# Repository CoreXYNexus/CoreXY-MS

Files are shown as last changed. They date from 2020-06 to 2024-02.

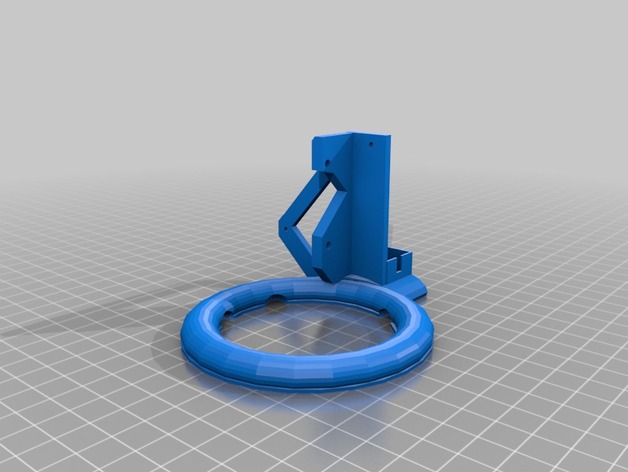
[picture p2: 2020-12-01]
STL/Other/Titan+Aero+Fan+shroud/images/5f8aa84927e1736dd930bd4a682ead06.png

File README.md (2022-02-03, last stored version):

# CoreXY-MS
A corexy printer using Makerslide, EXOSlide with Duet 3 6HC and 1LC using a Raspberry Pi 4.

August 2020: Upgraded to a Duet 3 6HC with 1LC.  Currently using in stand alone, no Pi.

A very old version is available at http://www.thingiverse.com/thing:1470253

https://creativecommons.org/licenses/by-sa/4.0/

https://youtu.be/llArYEVT2ow with Duet 2.
https://www.youtube.com/watch?v=qqqCqKSmpecVideo with the Duet 3.

All the horizontal extrusions, and the horizontal makerslide ends are tapped for 5mm.
Vertical 2020 is drilled with a 5.5mm bit for access to the screws that hold everything together. Four in the top and two in the bottom. Use drillguide.stl for drilling the holes.

Additional information can be found in the scad files. Include files are expected to be in a folder called inc in the folder with the printer's scad files.
In the top extrusions, I put 8 tnuts in each channel, the rest four in each. Use a short screw in a unused one to hold them to one side to quiet the rattle they can make while printing.

Spool holder: 300mm 2020 with two screw access holes in the bottom to mount it on the top rear 2040 and a 8mm hole in the top for a 8mm threaded rod long enough to hold a spool on each side. Using http://www.thingiverse.com/thing:1647748 to hold the spools.  The horizontal 2020 300mm long to hold filament guides for each spool.

On the bearing brackets from the top: M5x50, bearing support, washer, 2xF625Z,2x washers,2x F625Z, M5 nut.

If you use metal couplers for the z-axis, use a 4mm ball bearing in between the TR8 and stepper motor shaft inside the coupler. The bearing will allow tilt without changing the length.

The Litemount.stl holds a 70mm LED ring in http://www.thingiverse.com/thing:8211 I used a LM2596 buck convertor to get the 12vdc to power the ring.

Alternate lighting method is to use a 5050 LED light string stuck to the bottom of the x axis makerslide.  For EXOSlide, use PlainLEDStripHolderEXO and two short pieces for led strip.

Blower.scad uses http://www.thingiverse.com/thing:387301

Feet: http://www.thingiverse.com/thing:15880
or
Wheels: https://www.amazon.com/gp/product/B07FM76212

The 400mm x 300mm 1/4" MIC-6 AL plate bed uses 2020 to support the bed, they're attached just like rest of the extrusions. I used three 45mm x 25mm x 9mm 6061 with a 5mm hole for the extrusion mount and tapped a 3mm hole to hold the bed. I used some silicon tubing for the bed spacers. I used two keenovo 200x300 600w 110vac silicon heaters, using the thermistor in the center and wired the ac in parallel to a SSR. The printer uses 11.28 amps until PID kicks in, while printing it uses about 5 amps.  For auto-leveling (3 z leadscrew), use a 2020 frame under the bed consisting of 2 425mm and 3 385mm.

Cover for the SSR: http://www.thingiverse.com/thing:1001385

Spool holder: http://www.thingiverse.com/thing:1647748

Parts cooling fan: 4040 blower or a berd air

FancapL.stl is for the power supply fan to make it blow to the side.

9/2021 - Added EXOSlide use for X-Carraige.

Uses:
		OPENSCAD https://www.openscad.org/downloads.html  Use version 2019.05 or later.

		BOSL2: https://github.com/revarbat/BOSL2
		
		NEMA17 from https://github.com/mtu-most/most-scad-libraries
		
		configuration.scad, metric.scad, fasteners.scad, functions.scad are from an old version of http://github.com/prusajr/PrusaMendel

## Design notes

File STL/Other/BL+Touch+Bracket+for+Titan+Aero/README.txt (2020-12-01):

BL Touch Bracket for Titan Aero by Celcius1 on Thingiverse: https://www.thingiverse.com/thing:3463051

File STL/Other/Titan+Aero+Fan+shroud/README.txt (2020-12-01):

Titan Aero Fan shroud by TexasJeep on Thingiverse: https://www.thingiverse.com/thing:2943061

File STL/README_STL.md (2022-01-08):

Contains the STL files for CXY-MSv1

May not contain a complete set.

Other contains parts made by someone else.

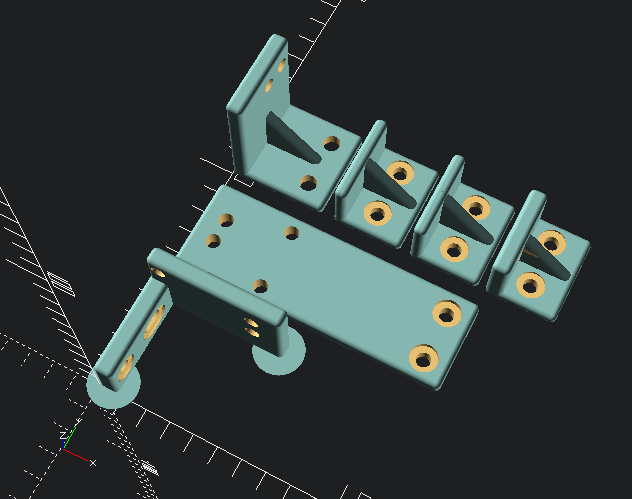
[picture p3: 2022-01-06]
Photos/SingleWirechain.png

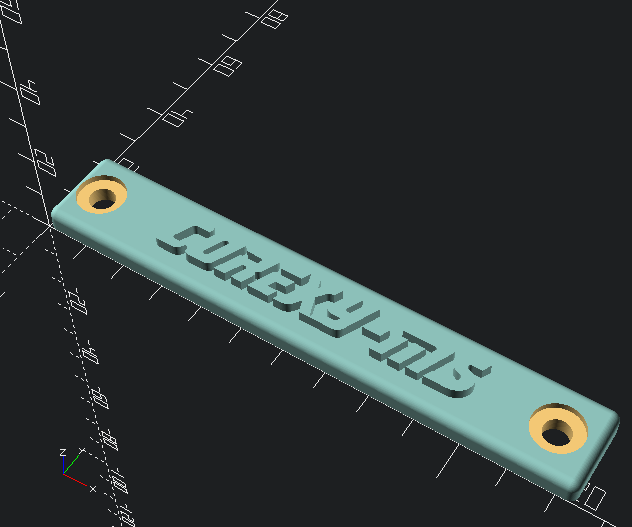
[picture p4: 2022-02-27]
Photos/Nameplate.png

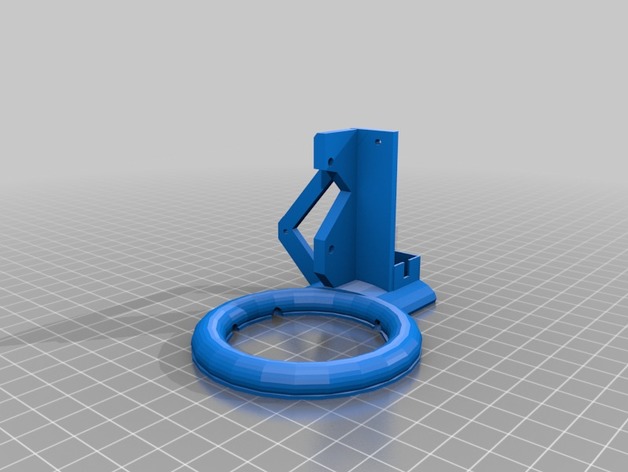
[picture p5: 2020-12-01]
STL/Other/Titan+Aero+Fan+shroud/images/f56a5410c23ab4886e00829ec24eeb07.png

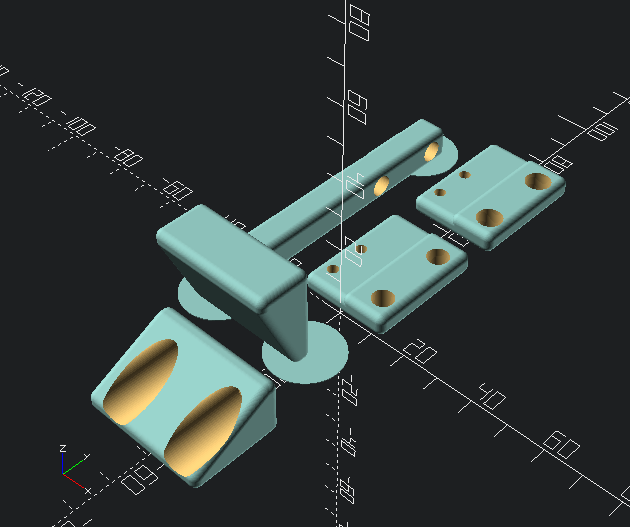
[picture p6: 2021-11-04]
Photos/EndstopsEXOSlide.png

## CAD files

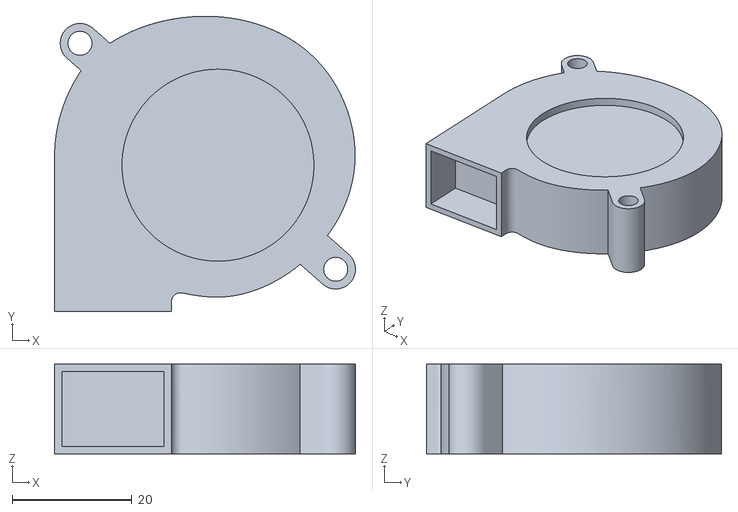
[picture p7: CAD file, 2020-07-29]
scad/5015_Blower_Fan.stl
50.2 x 49.2 x 15.0

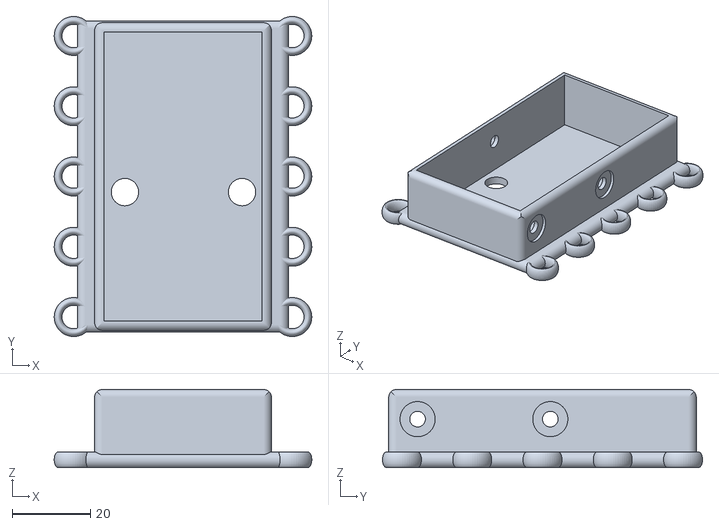
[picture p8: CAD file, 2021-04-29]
STL/Other/BerdAir Motor+Anti_Vibration+Ball+&+Floating+Mount/files/Air_Pump_Float_Mount.stl
66.0 x 82.0 x 20.0

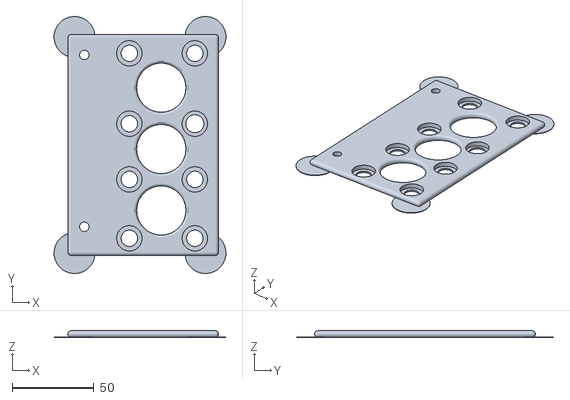
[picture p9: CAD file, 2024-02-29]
STL/Other/BerdAirPump/Berd Air Flat Base Mount.stl
105.0 x 157.0 x 4.00

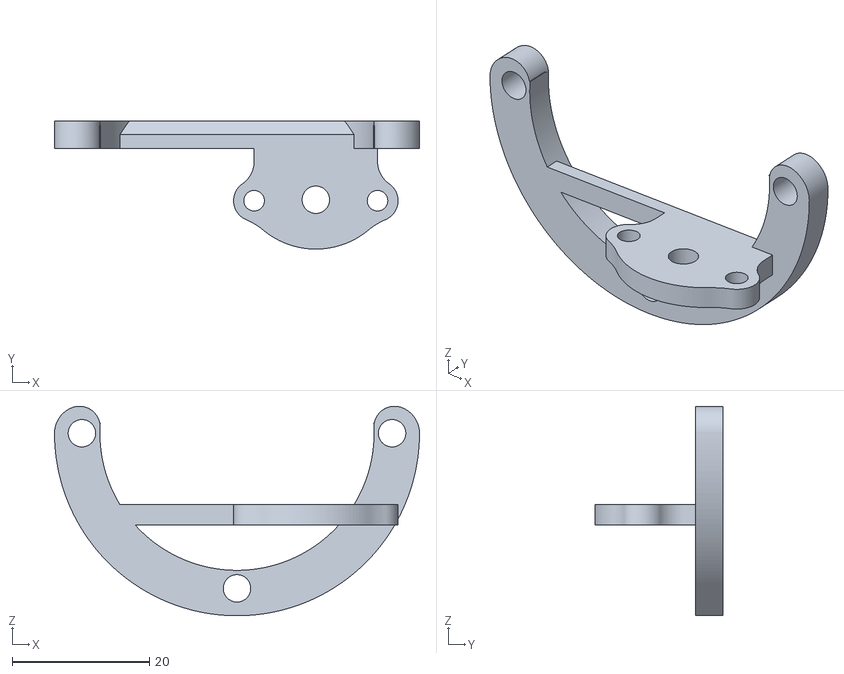
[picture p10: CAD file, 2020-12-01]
STL/Other/BL+Touch+Bracket+for+Titan+Aero/files/BL_Touch_Aero_Volcano.stl
53.2 x 18.7 x 30.6

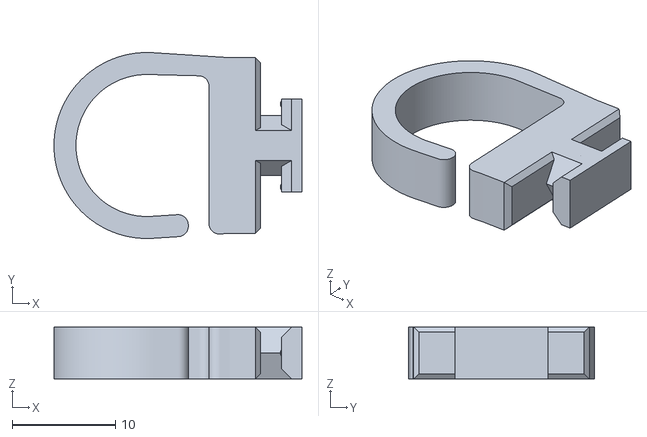
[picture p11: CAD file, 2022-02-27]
STL/Other/Cable_bundler.stl
24.0 x 18.0 x 5.02

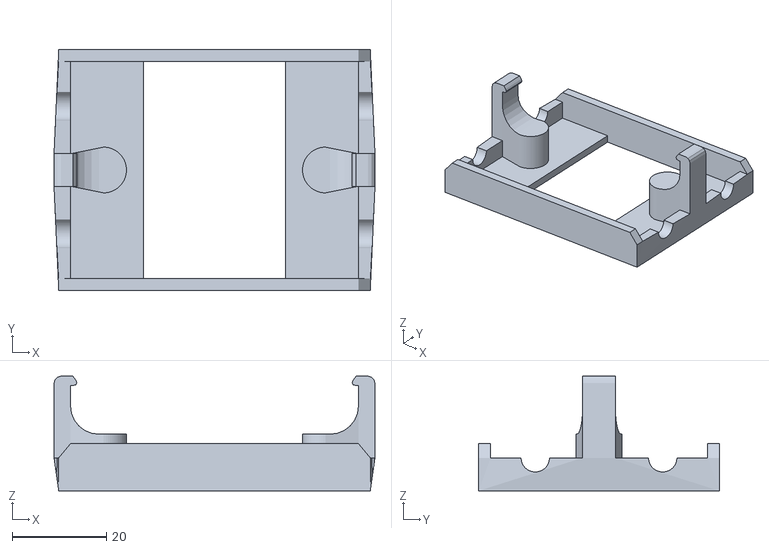
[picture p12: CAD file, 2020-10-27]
STL/Other/SSR_relay_cover_with_clips_and_cutouts/files/ssr_cover_clips_cutouts.stl
68.0 x 51.0 x 24.3

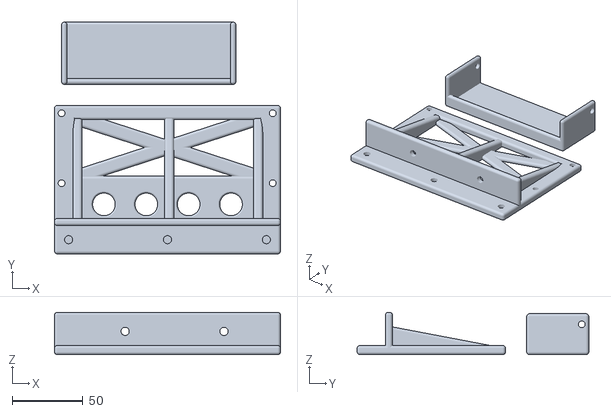
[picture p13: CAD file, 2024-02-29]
STL/PS Meanwell LRS-350-24 Mount.stl
160.0 x 164.0 x 30.0

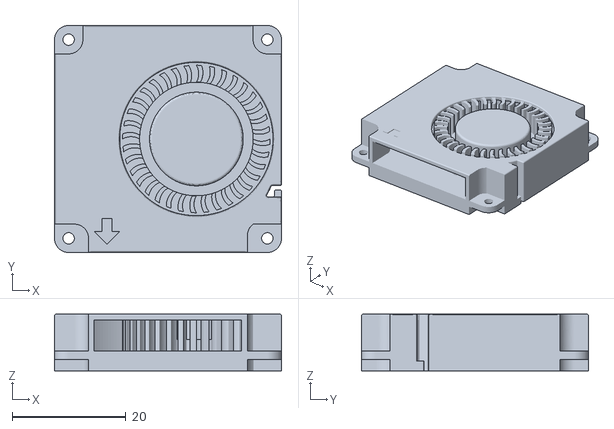
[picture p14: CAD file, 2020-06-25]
scad/4010_Blower_Fan_v2.stl
40.0 x 40.0 x 10.0

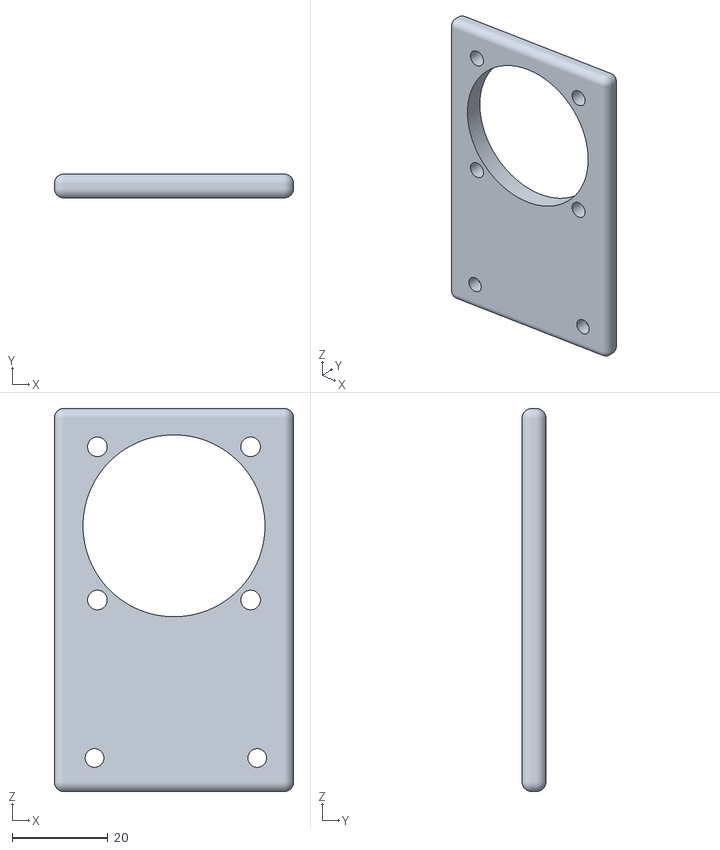
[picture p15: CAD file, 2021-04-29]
STL/Other/BerdAir Motor+Anti_Vibration+Ball+&+Floating+Mount/files/Air_Pump_Anti-Shock_Base.stl
50.0 x 5.00 x 80.0

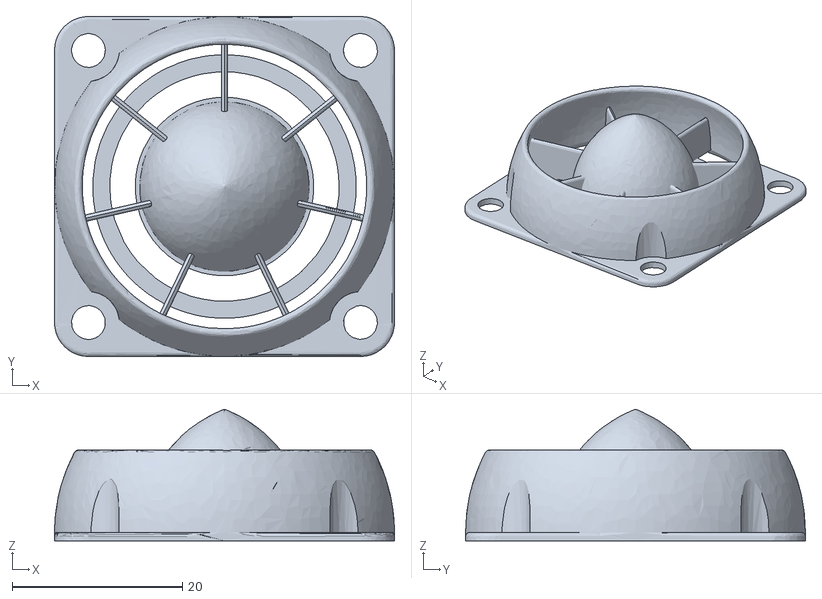
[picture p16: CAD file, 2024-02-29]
STL/Other/BerdAirPump/Berd_Air_Pump_Fan_Grill (1).stl
40.0 x 40.0 x 15.5

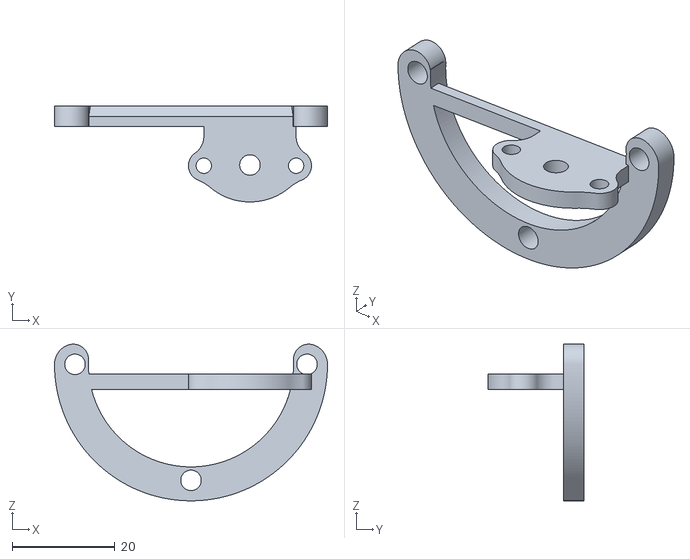
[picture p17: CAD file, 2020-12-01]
STL/Other/BL+Touch+Bracket+for+Titan+Aero/files/BL_Touch_Aero_V6.stl
53.2 x 18.7 x 30.6

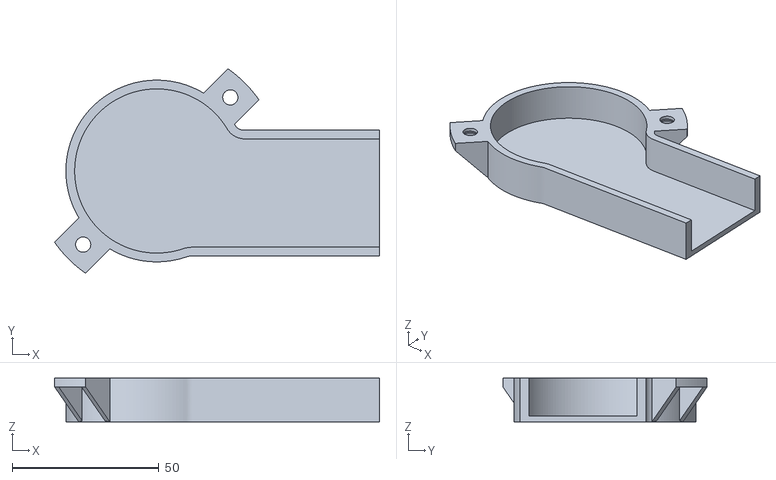
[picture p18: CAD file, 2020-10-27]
STL/Other/FanCap_Long.stl
110.9 x 69.8 x 15.0

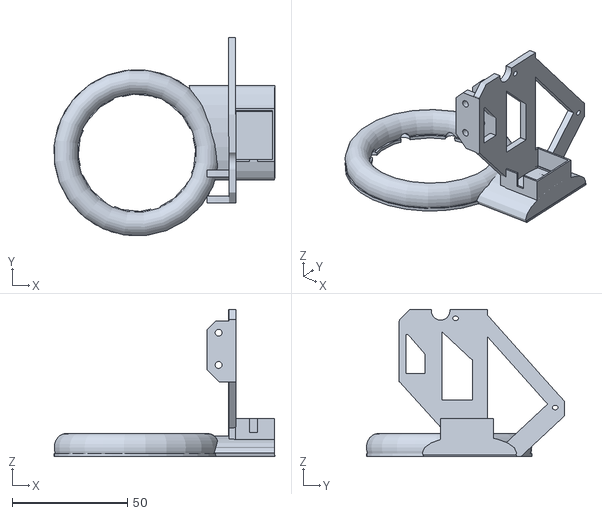
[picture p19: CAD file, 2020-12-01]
STL/Other/Titan+Aero+Fan+shroud/files/Titan_Aero_Fan_Shroud_-_Creality_X.stl
96.0 x 86.1 x 64.0

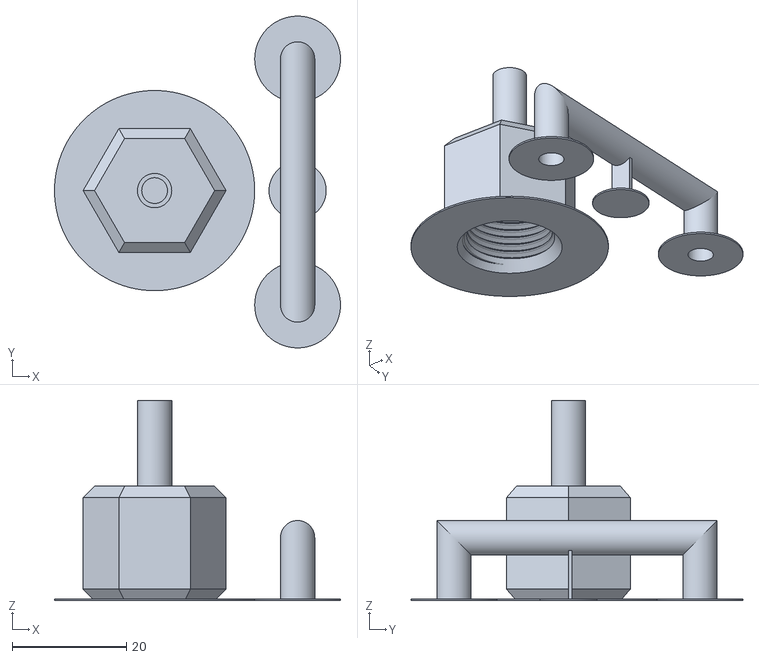
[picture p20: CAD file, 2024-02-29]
STL/PipeToTubing.stl
50.0 x 58.0 x 35.0

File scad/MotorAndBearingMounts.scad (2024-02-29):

 /////////////////////////////////////////////////////////////////////////////////////////
// MotorAndBearingMounts.scad - hold the motors, belts & bearing bracket inside the frame
/////////////////////////////////////////////////////////////////////////////////////////
// created 7/5/2016
// last update 1/22/22
/////////////////////////////////////////////////////////////////////////////////////////
// https://creativecommons.org/licenses/by-sa/4.0/
/////////////////////////////////////////////////////////////////////////////////////////////////////////////////////////////
// 7/7/16	- added built-in spacer to the bearing_bracket
// 7/14/16	- adjusted 2002 mounting holes to have motor mount clear the makerslide rails
//			  mirrored bearing() for other side and it now makes all four parts
// 7/15/16	- Made the FrontBearingBracket() bearing screw hole to be tap sized or not
// 7/16/16	- Made makerslide rail notch in FrontBearingBracket() optional
//            Added nut hole to FrontBearingBracket() to use M5x50 screw
// 7/18/16	- Made motor_mount taller above the makerslide
// 7/19/16	- Changed 3rd wall to a diagonal support on MotorMount() and removed notch on
//			  the non-makerslide wall
// 7/20/16	- Moved upper belt stepper motor up 10mm
// 8/23/16	- Added Vthickness & Tthickness for BearingSupport()
// 1/10/17	- Added labels to motor mounts and colors to preview for easier editing
// 2/14/17	- Adjusted bearing screw hole in BearingSupport, noticed that it's off by 2mm when I replaced the
//			  makerslide with a 2040 to use the makerslide for a three motor z axis.
//			  Tapered the spacer on the bearing_bracket and added L/R labels.
// 7/13/18	- Added a cube showing a 200x200 bed to all()
// 8/19/18	- OpenSCAD 2018.06.01 for $preview
// 12/8/18	- Changed stepper motor mount to slots for belt adjustment, adjusted diagonal supports
//			  on the stepper motor mounts
// 2/28/19	- Bugfix in all() and FrontBearingBracket()
// 4/16/19	- Changed the angle support for the motor mounts to match the Z motor mounts
//			  Changed the BearingSupport() to match the motor mount notch supports
// 7/2/19	- Made the labels tilted a bit to print better, updated mirror() to 2019.05 version
// 5/16/20	- Rounded the end of the bearing bracket end and reduced the width that connects to the 2020
// 8/8/20	- Changed the supports for the BearingSupport()
// 10/17/20	- Can now use 5mm inserts
// 4/1/21	- Added an adjustable front bearing mount
// 4/24/21	- Added thrust washer to front bearing mount base
// 10/16/21	- Changed support on MotorMount()
// 1/4/22	- BOSL2
// 1/22/22	- Imporoved motor mount supports
// 5/2/23	- Enlarged adjustability on MotorMount()
/////////////////////////////////////////////////////////////////////////////////////////
// NOTE: Bearing position in FrontBearingBracket() must match stepper motor shaft in MotorMount()
//       If the motors get hot, print it from something that can handle it
//       Bearing stack is 5mm washer,F625Z,F625Z,5mm washer,5mm washer,F625Z,F625Z,5mm washer,
//       M5x50, and a 5mm brass insert
//		 Motor mounts have two holes on the makerslide side, to allow the makerslide to be installed either way.
//		 Adjustable front bearing has the motor adjustable, since you may not get the belts the same length.
//		 Used M3x40 screw in the bearing holder, held in with a M3 mut. Each base uses a M3x10 Thrust washer.
// --------------------------------------------------------------------------------------
//		 Taller motor_mount on left side rear.
//		 NON-adjustable bearing brackets at inside front corners & supports on outside
//		 Install one M5 brass insert in each bearing bracket
//		 Print motor mounts with ABS or PETG
/////////////////////////////////////////////////////////////////////////////////////////
include <bosl2/std.scad>
use <inc/nema17.scad>
include <inc/brassinserts.scad>
$fn=100;
/////////////////////////////////////////////////////////////////////////////////////////
// vars for this file
b_posY = 29.5;				// bearing position X
b_posX = 20;				// bearing position Y
b_height = 10;				// amount to raise bearings
F625ZDoulbleStack = 11.78;	// just the length of two washers & two F625Z bearings
F625ZDiameter = 18; 		// diameter of the f625z bearing
LayerThickness = 0.35;		// layer thickness used to print
Vthickness = 7;				// thickness of bearing support vertical section
Tthickness = 5;				// thickness of bearing support top and fillet
Use3mmInsert=1;
LargeInsert=1;
Use5mmInsert=1;
Knob_Diameter=nut3*3;
Knob_Height=3;
WasherThickness=1;
ThrustBrearingDiameter=10;	// M3 thrust bearing
TextFont="Liberation Sans";
/////////////////////////////////////////////////////////////////////////////////////////

//NonAdjustableBearingMountSet(); // all the needed parts
//AdjustableFrontBearingMountSet(); // all the needed parts
//AdjustableFrontBearingMount(0,0);
//AdjustingKnob();
MotorMount();
translate([70,0,0]) MotorMount(1);

/////////////////////////////////////////////////////////////////////////////////////////

module NonAdjustableBearingMountSet() {
	translate([0,-5,0]) MotorMount(1);
	translate([35,60,-2.5]) rotate([0,0,0]) FrontBearingBracket(0,"Right");
	translate([80,-30,F625ZDoulbleStack*2+b_height+40]) rotate([0,180,0]) BearingSupport(2,0);
	translate([0,65,0]) MotorMount(0);
	translate([75,20,-2.5]) rotate([0,0,0]) mirror([1,0,0]) FrontBearingBracket(0,"Left"); // mirror it for the other side
}

///////////////////////////////////////////////////////////////////////////////////////////////////////

module AdjustableFrontBearingMountSet() {
	translate([0,-33,2.55]) MotorMount(1,1);
	translate([0,86,2.55]) MotorMount(0,1);
	rotate([0,-90,0]) AdjustableFrontBearingMount(1,0);
	translate([95,0,0]) rotate([0,-90,0]) AdjustableFrontBearingMount(1,0);
	translate([-25,10,0]) AdjustingKnob();
	translate([-5,10,0]) AdjustingKnob();
}

/////////////////////////////////////////////////////////////////////////////////////////

module AdjustableFrontBearingMount(DoBase=1,Fit=0) {
	difference() { // vertical
		union() {
			translate([0,0,45]) color("cyan")
				cuboid([Vthickness,F625ZDiameter,F625ZDoulbleStack*2+b_height-2],rounding=1,p1=[0,0]);
			translate([0,0,45-WasherThickness]) color("white") cuboid([34,F625ZDiameter,Tthickness-1],rounding=1,p1=[0,0]);
			translate([33,9,F625ZDoulbleStack*2+b_height+11.45-WasherThickness+2]) color("red")
				cyl(h=Tthickness-1,d=F625ZDiameter,rounding=1); // bottom
			translate([0,0,F625ZDoulbleStack*2+b_height+38]) color("blue") 
				cuboid([34,F625ZDiameter,Tthickness],rounding=1,p1=[0,0]);
			translate([33,9,F625ZDoulbleStack*2+b_height+40.5]) color("cyan")
				cyl(h=Tthickness,d=F625ZDiameter,rounding=1); // top
			translate([0,0,45]) color("green") cuboid([20,Tthickness-1,30],rounding=2,p1=[0,0]);
			translate([0,14,45]) color("lightgreen") cuboid([20,Tthickness-1,30],rounding=2,p1=[0,0]);
			translate([33,9,43]) color("green") cyl(h=4,d1=Yes5mmInsert(Use5mmInsert)+1,d2=F625ZDiameter); // M5 insert
			translate([33,9,78]) color("red") cyl(h=4,d1=F625ZDiameter-0.5,d2=screw5+1);
		}
		translate([Vthickness+26,9,F625ZDoulbleStack+b_height+30]) color("lightgray") cylinder(h=50,d=screw5); // top
		translate([Vthickness+26,9,F625ZDoulbleStack+b_height-5]) color("gray")
			cylinder(h=50,d=Yes5mmInsert(Use5mmInsert)); // bottom
		translate([Vthickness+26,9,F625ZDoulbleStack*2+b_height+42]) color("blue") cylinder(h=5,d=screw5hd);
		translate([-25,9,F625ZDoulbleStack*2+b_height+27.5]) rotate([0,90,0]) color("plum")
			cylinder(h=50,d=Yes3mmInsert(Use3mmInsert));
	}
	if(DoBase) {
		if(Fit) translate([0,0,-1]) AdjustableFrontBearingMountBase();  // fit parts
		else  translate([5,27,-5]) AdjustableFrontBearingMountBase();
	}
}

//////////////////////////////////////////////////////////////////////////////////////////////////////////////////////////
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

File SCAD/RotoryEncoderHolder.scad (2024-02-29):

////////////////////////////////////////////////////////////////////////////////////////////////////////
// RotoryEncoderHolder.scad
//////////////////////////////////////////////////////////////////////////////////////////////////////////
// Created: 5/14/2023
// Last Update: 5/14/23
/////////////////////////////////////////////////////////////////////////////////////////////////////////////////////////
// https://creativecommons.org/licenses/by-sa/4.0/
/////////////////////////////////////////////////////////////////////////////////////////////////////////////////////////////
include <inc/screwsizes.scad>
include <BOSL2/std.scad>
//include <inc/brassinserts.scad>
///////////////////////////////////////////////////////////////////////////////////////////////////////////////////////
$fn=100;
LayerThickness=0.3;
RiserHeight=45;
BoltCircleDiameter=30;
///////////////////////////////////////////////////////////////////////////////////////////////////////////////////////////

RotoryEncoderHolder();

/////////////////////////////////////////////////////////////////////////////////////////////////////////////////////

module RotoryEncoderHolder() {
	difference() {
		color("cyan") hull() { // base
			cyl(h=5,d=10,rounding=2);
			translate([45,0,0]) cyl(h=5,d=50,rounding=2);
			translate([90,0,0]) cyl(h=5,d=10,rounding=2);
		}
		translate([45,0,-0.01]) color("gold") cyl(h=5,d=41,rounding1=-2); // round bottom rotary hole
		translate([45,-45/2,0]) color("pink") cuboid([10,10,10]); // side slot
		BaseSlotRounding();
		BaseHoles();
	}
	Riser();
	RotaryMountFlange();
}

///////////////////////////////////////////////////////////////////////////////////////////////////////////////////////

module BaseHoles() {
	translate([2,0,0]) color("red") hull() { // screw slot
		translate([0,0,0]) cyl(h=10,d=screw5);
		translate([10,0,0]) cyl(h=10,d=screw5);
	}
	translate([78,0,0]) color("blue") hull() { // screw slot
		translate([0,0,0]) cyl(h=10,d=screw5);
		translate([10,0,0]) cyl(h=10,d=screw5);
	}
	translate([45,0,0]) color("white") cyl(h=20,d=41); // base hole
}

//////////////////////////////////////////////////////////////////////////////////////////////////////////////////////

module BaseSlotRounding() {
	translate([45-6,-45/2-4,0]) color("lightgray") rotate([0,90,0]) cuboid([5,5,2],rounding=-2,edges=[TOP]); // slot
	translate([45-6,-45/2,-5]) color("lightgray") rotate([0,90,0]) cuboid([5,5,2],rounding=-2,edges=[TOP]);
	translate([45+6,-45/2-4,0]) color("lightgray") rotate([0,-90,0]) cuboid([5,5,2],rounding=-2,edges=[TOP]);
	translate([45+6,-45/2,-5]) color("lightgray") rotate([0,-90,0]) cuboid([5,5,2],rounding=-2,edges=[TOP]);
	translate([45-6,-45/2+6,0]) color("lightgray") rotate([0,90,0]) cuboid([5,5,2],rounding=-2,edges=[TOP]); // slot
	translate([45+6,-45/2+6,0]) color("lightgray") rotate([0,-90,0]) cuboid([5,5,2],rounding=-2,edges=[TOP]);
}

//////////////////////////////////////////////////////////////////////////////////////////////////////////////////////////

module Riser() {
	difference() { // riser
		translate([RiserHeight,0,RiserHeight/2]) color("purple") cyl(h=RiserHeight,d=49); // outer
		translate([RiserHeight,0,RiserHeight/2]) color("white") cyl(h=RiserHeight+5,d=41); // inner
		translate([RiserHeight,-RiserHeight/2,RiserHeight/2]) color("pink") rotate([0,90,0]) cuboid([50,10,10]); // side slot
		translate([RiserHeight,-RiserHeight/2+2,RiserHeight/2]) color("gray") rotate([0,90,90])
			cuboid([50,10,2],rounding=-2,edges=[TOP]); // side slot
		translate([RiserHeight,-RiserHeight/2-0.5,RiserHeight/2]) color("gray") rotate([0,90,-90])
			cuboid([50,10,2],rounding=-2,edges=[TOP]); // side slot
		translate([RiserHeight,0,0]) color("gold") cyl(h=5,d=41,rounding1=-2); // round base rotary hole
	}
}

////////////////////////////////////////////////////////////////////////////////////////////////////////////////////////

module RotaryMountFlange() {
	difference() { // rotary mount
		translate([RiserHeight,0,RiserHeight]) color("khaki") cyl(h=5,d=49,rounding=2);
		translate([RiserHeight,0,RiserHeight]) color("blue") cyl(h=10,d=20.5);
		translate([45,0,40]) color("red") BoltCircle(BoltCircleDiameter);
	}
	translate([RiserHeight,0,RiserHeight-2.5]) color("gray") cyl(h=LayerThickness*2,d=45); // support
}


//////////////////////////////////////////////////////////////////////////////////////////////////////////////////////////

module BoltCircle(Dia=30,h=20) {
linear_extrude(h)
	for(i = [-1 : 1])
		rotate(i * 120) translate([0, Dia / 2]) circle(d = screw3);
}

/////////////////////////////////////////////////////////////////////////////////////////////////////////////////////////

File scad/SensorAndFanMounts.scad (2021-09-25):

/////////////////////////////////////////////////////////////////////////////////////////////////////
// SensorAndFanMounts.scad
/////////////////////////////////////////////////////////////////////////////////////////////////////
// created: 6/2/1019
// last update: 9/21/21
////////////////////////////////////////////////////////////////////////////////////////////////////
// 6/2/19	- Separated from single_titan_extruder_mount.scad
// 4/12/20	- Made the mount to extruder plate the same for Proximity & BLTouch
// 8/4/20	- Adjsuted the sensor mount holes to the extruder platform
// 8/17/20	- Copied and edited from M-Max and added an adjustable mount for dc42's ir sensor
// 8/30/20	- Added an adjustable BLTouch mount
// 10/15/20	- Added IR mount for titan aero (mounts on printed extruder mount)
// 9/18/21	- Added a mount for a bmg extrude
////////////////////////////////////////////////////////////////////////////////////////////////////
include <CoreXY-MSv1-h.scad>
use <inc/corner-tools.scad>
use <fanduct_v3.scad>
include <inc/brassinserts.scad>
include <BOSL2/std.scad>
/////////////////////////////////////////////////////////////////////////////////////////////////
//*****************************************************
// adjustable proximity mount need beefing up 9/19/20
//*****************************************************
$fn=100;
psensornut = 28; 	// size of proximity sensor nut
FanSpacing = 32;	// hole spacing for a 40mm fan
PCfan_spacing = 47;	//FanSpacing+15;
DuctLength=25; 		// set length of 50150 fan duct
Thickness = 6.5;
MHeight = 6;
MWidth = 60;
FHeight = 10;
MountingHoleHeight = 60; 	// screw holes may need adjusting when changing the front to back size
ExtruderOffset = 18;		// adjusts extruder mounting holes from front edge
IRSpacing=spacing;
LayerThickness=0.3; // layer thickness
Spacing = 17; 			// ir sensor bracket mount hole spacing
//------------------------------------------------------------------------------------------------
Use2p5mmInsert=1;
Use3mmInsert=1; // set to 1 to use 3mm brass inserts
LargeInsert=1;
//Use4mmInsert=1; // set to 1 to use 4mm brass inserts
//Use5mmInsert=1; // set to 1 to use 5mm brass inserts
//-----------------------------------------------------------------------------------------
StepperHoleOffset=31;
////////////////////////////////////////////////////////////////////////////////////////////////////////////

//ProximityMount(6); // arg is shift up/down (min:2)
//BLTouchMount(2,20,1);	// 1st arg:type; 2nd: shift; BLTouch v3.1
//IRAdapter(0,0);
//IRAdapterAero(0);
//Spacer(3,7);
BMGBLTMount(5);

///////////////////////////////////////////////////////////////////////////////////////////////////////////

module BMGBLTMount(Offset=5) {
	difference() {
		union() {
			translate([0,-Offset,0]) color("cyan") cuboid([StepperHoleOffset+10,10+Offset,9],rounding=2,p1=[0,0]);
			//translate([0,-5-Offset,4]) color("plum") cuboid([StepperHoleOffset+10,10+Offset,5],rounding=2,p1=[0,0]);
			translate([0,-Offset,0]) color("khaki") cuboid([StepperHoleOffset+10,5,25],rounding=2,p1=[0,0]);
		}
		translate([(StepperHoleOffset+10)/2,-Offset,-8]) color("red") rotate([90,0,0])  cyl(l=8, d=30, rounding=2);
		translate([5,5,-5]) color("blue") cylinder(h=20,d=screw3);
		translate([StepperHoleOffset+5,5,-5]) color("red") cylinder(h=20,d=screw3);
		translate([5,5,8]) color("red") cylinder(h=5,d=screw3hd);
		translate([StepperHoleOffset+5,5,8]) color("blue") cylinder(h=5,d=screw3hd);
		translate([20,-Offset,0]) rotate([90,90,0]) rotate([0,0,90]) BLTouch_Holes(2,Yes2p5mmInsert(Use2p5mmInsert));
	}
}

///////////////////////////////////////////////////////////////////////////////////////////////////////////////////////////

module Spacer(Qty=1,Thickness=5,Screw=screw3,BottomSize=3) {
	for(x = [0:Qty-1]) {
		translate([0,x*15,0]) difference() {
			color("cyan") hull() {
				cylinder(h=0.5,d=Screw*BottomSize);
				translate([0,0,Thickness]) cylinder(h=1,d=Screw*2);
			}
			translate([0,0,-2]) color("plum") cylinder(h=Thickness+5,d=Screw);
		}
	}
}

//////////////////////////////////////////////////////////////////////////////////////////////////////////////////////

module Short_Motor_Version(Duct=0,Move=0,Raise=0,Back=0,Offset=0) {
	FanBlowerMount(Move,Raise,Back);
	if(Duct) translate([0,12,0]) color("red") FanDuct_v3(DuctLength);
}


/////////////////////////////////////////////////////////////////////////////////////////////////////////////////////////

module BracketMount_v2(Move=0) {
	translate([3,10,FHeight/4+0.3]) rotate([90,0,0]) color("red") cylinder(h = 18,r = screw3/2,$fn=50);
	translate([3,1,FHeight/4+0.3]) rotate([90,0,0]) color("gray") cylinder(h = 18,r = screw3hd/2,$fn=50);
	translate([3+PCfan_spacing,10,FHeight/4+0.3]) rotate([90,0,0]) color("blue") cylinder(h = 18,r = screw3/2,$fn=50);
	translate([3+PCfan_spacing,1,FHeight/4+0.3]) rotate([90,0,0]) color("plum") cylinder(h = 18,r = screw3hd/2,$fn=50);
}

//////////////////////////////////////////////////////////////////////////////////////////////////////

module FanBlowerMount(Move=0,Raise=0,Back=0,X=0,Y=0,Z=0,Spacer=0,Offset=0) {
	if(Spacer) {
		difference() {
			translate([Move+6,-30+Back,0]) color("gray") cubeX([21,21-Back,Raise+Z+5],1);
			RemoveForBlower(Move+6,Raise,Spacer);
			translate([Move+X,-14-Back+Y,Raise+Z]) rotate([0,90,0]) color("purple") cylinder(h=42,r=screw4/2,$fn=50);
			translate([Move+2,-40+Back,10]) rotate([-45,0,0]) color("black") cube([30,30,10]);
		}
		//difference() {
		//	translate([Move+6,Offset+2,0]) color("lightgray") cubeX([21,Offset,Thickness],1);
		//	translate([0,0,0.5]) BracketMount(Move);
		//	translate([5,-5-Offset,0]) color("plum") cube([30,20,20]);
		//}
	} else {
		difference() {
			translate([Move,-16+Back,0]) color("gray") cubeX([21,21-Back,Raise+4],2);
			RemoveForBlower(Move,Raise);
			translate([Move+X-3,-Back+Y,Raise+Z]) rotate([0,90,0]) color("purple") cylinder(h=42,r=screw4/2,$fn=50);
			translate([Move-5,-29+Back,9]) rotate([-45,0,0]) color("black") cube([30,30,10]);
		}
	}
}

///////////////////////////////////////////////////////////////////////////////////////////////////////////////

module RemoveForBlower(Move=0,Raise=0,Spacer=0) {
	if(Spacer) {
		translate([Move+3,-57,-10]) color("yellow") cubeX([15,45,Raise*2],1);
		//translate([Move+3,-15.5,-17]) rotate([35,0,0]) color("lightgreen") cubeX([15,15,15],1);
	} else {
		translate([Move+3,-45,-10]) color("yellow") cubeX([15,45,Raise*2],1);
	}
}

////////////////////////////////////////////////////////////////////////////////////////////////////////////////////////

module FanMountHoles(Screw=screw3,Left=1) {	// fan mounting holes
	if(Left) {
		translate([-extruder/2-22,-heightE/2 - 1.8*wall,heightE - extruder_back - fan_spacing/2 + fan_offset])
			rotate([0,90,0]) color("pink") cylinder(h = 3*(ExtruderThickness+screw_depth),d = Screw);
		translate([-extruder/2-22,-heightE/2 - 1.8*wall,heightE - extruder_back + fan_spacing/2 + fan_offset])
			rotate([0,90,0]) color("skyblue") cylinder(h = 3*(ExtruderThickness+screw_depth),d = Screw);
	} else { // one side fan mounting holes
		translate([-extruder/2+35,-heightE/2 - 1.8*wall,heightE - extruder_back - fan_spacing/2 + fan_offset])
			rotate([0,90,0]) color("pink") cylinder(h = ExtruderThickness+screw_depth,d = Screw);
		translate([-extruder/2+35,-heightE/2 - 1.8*wall,heightE - extruder_back + fan_spacing/2 + fan_offset])
			rotate([0,90,0]) color("skyblue") cylinder(h = ExtruderThickness+screw_depth,d = Screw);

	}
	translate([-38,-44.5,20]) rotate([0,90,0]) color("plum") nut(nut3,5);	// nut trap for fan
	translate([-38.5,-44.5,52]) rotate([0,90,0]) color("blue") hull() {	// nut trap for fan
		nut(nut3,2.55);
		translate([0,8,0]) nut(nut3,2.5);
	}
}

////////////////////////////////////////////////////////////////////////////////////////////////////////////////////////

module FanMountHolesPlatform(Screw=screw3,Left=1) {	// fan mounting holes
	if(Left) {
		translate([-extruder/2-22,-heightE/2 - 1.8*wall,heightE - extruder_back - fan_spacing/2 + fan_offset])
			rotate([0,90,0]) color("pink") cylinder(h = 3*(ExtruderThickness+screw_depth),d = Screw);
		translate([-extruder/2-22,-heightE/2 - 1.8*wall,heightE - extruder_back + fan_spacing/2 + fan_offset])
			rotate([0,90,0]) color("skyblue") cylinder(h = 3*(ExtruderThickness+screw_depth),d = Screw);
	} else { // one side fan mounting holes
		translate([-extruder/2+35,-heightE/2 - 1.8*wall,heightE - extruder_back - fan_spacing/2 + fan_offset])
			rotate([0,90,0]) color("pink") cylinder(h = ExtruderThickness+screw_depth,d = Screw);
		translate([-extruder/2+35,-heightE/2 - 1.8*wall,heightE - extruder_back + fan_spacing/2 + fan_offset])
			rotate([0,90,0]) color("skyblue") cylinder(h = ExtruderThickness+screw_depth,d = Screw);

	}
}

////////////////////////////////////////////////////////////////////////////////////////////////////////////////////////
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

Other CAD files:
STL/Other/BerdAir Motor+Anti_Vibration+Ball+&+Floating+Mount/images/large_display_Infinity_Sword_Support.stl
STL/Other/BerdAir Motor+Anti_Vibration+Ball+&+Floating+Mount/images/small_preview_Air_Pump_Anti-Shock_Mount_.stl
STL/CameraMount.stl
STL/Other/BerdAir Motor+Anti_Vibration+Ball+&+Floating+Mount/files/mount.stl
SCAD/SensorMounts.scad
SCAD/Bread Air Base Mount.scad
SCAD/CornerBrace.scad
SCAD/Coupler.scad
SCAD/DrillGuides.scad
SCAD/DualHotend.scad
SCAD/E3DV65150Adapter.scad
SCAD/Endstops.scad
SCAD/FanAdapters.scad
SCAD/HeaderSpacer.scad
SCAD/Hose_Adaptor.scad
SCAD/LEDRing.scad
SCAD/LeadScrewTop.scad
SCAD/NEOPixelStrip.scad
SCAD/NozzleCleaner.scad
SCAD/PIPowerSwitch.scad
SCAD/PS Meanwell LRS-350-24 Mount.scad
SCAD/PipeToTubing.scad
SCAD/PlainLEDStripHolderEXO.scad
SCAD/ResetButton.scad
SCAD/SpoolHolderBearing.scad
SCAD/TitanAero.scad
SCAD/XWireChain.scad
SCAD/yBeltClamp.scad
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

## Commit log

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2018-07-15 Updated x carriage titan belt
    Missing titan mount on wade;s style extruder mount
    [Corexy-x-carriage.scad]
2018-08-19 updates and a dual hotend setup
    updates
    Added DualTitan.scad for dual Titan, direct and bowden
    [Corexy-x-carriage.scad, Corexy-z-axis.scad, DualTitan.scad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]
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2018-09-04 Added a dual hotend
    Added a dual htoend using Titan extruders and other updates
    [Corexy-x-carriage.scad, DualTitan plate for se .stl, DualTitan.scad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]
2018-10-10 Dual Titan fixes
    Dual Titan fixes and updates
    [DualTitan.scad, NewDualTitan no sensor bracket no extruder.stl, NewTitan Dual Extruder Mounts.stl]
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2018-12-18 Update - rename
    Filename change and removal of STL files. Filename format allows Slic3r PE 1.42 to send to the Duet without editing the filename.
    [CXY-MSv1 Nameplate.stl, CoreXY--X-Carriage.scad, CoreXY-MSv1-h.scad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]
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2018-12-21 Update
    Added support for the lower printed hole for the bearing in the pivot. Added two holes for the end of the 2040.
    [Z-Bed_Leveling_Pivots-Bearing-x1.stl, Z-Bed_Leveling_Pivots.scad]
2018-12-23 Updates
    Testing independent trhee Z motor setup for bed leveling. Added a PI3 w/pi camera in a case mount.
    [CoreXY-Z-axis-Drive.scad, PanelDue-Mount-Top-2040.stl, WebCam-Mount-PI.stl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]
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2019-01-31 Update
    Fixed/added a few mounting holes
    Adjusted fan adapter position on titan()
    Changed titan2() name to titan_bowden_mount()
    Removed titan3()
    Ziptie hole on blt_mount()
    Fixed z_pivots() so all parts are on the same z0
    Added z_pivot_2040_v2(), it uses less plastic, it only attaches to the end of a 2040
    Added screw size to extrusion slots option to z_pivot_2040()
    [CoreXY--X-Carriage.scad, Z-Bed_Leveling_Pivot_on_2040.stl, Z-Bed_Leveling_Pivots-x1.stl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]
2019-02-07 Update
    Changed to OPENSCAD 2019-01-RC2
    CoreXY-Z-axis-drive.scad:
    Adjusted notches on motor mount. Fixed colors in side_support(). Changed NEMA17 holes to a set motor position, shaft_offset is now taken into account with z_shift. Added M3 version to plates().
    [CoreXY-Z-axis-Drive.scad, CoreXY-titan_blt_mount.stl, Parts-Blower.scad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]
2019-02-14 Update
    Moved BeltHolder.scad into CoreXY--X-Carriage.scad. Renamed BeltHolder.scad height to LoopHeight.
    Redid Psrts-Blower.scad for the latest version of the titan extruder/hotend mount.
    [CoreXY--X-Carriage.scad, CoreXY--X-Carriage.stl, CoreXY-Motor-x2.stl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]
2019-02-25 Updates
    Updates, bug fixes
    [CarriageBeltDrive.stl, CoreXY--X-Carriage.scad, Parts-Blower-Adapter-6o.stl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]
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2019-03-26 Updates
    Bug fixes and some modifications
    [CXY-MSv1 Nameplate.scad, CoreXY--X-Carriage.scad, CoreXY-X-Carriage.scad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]
2019-04-06 Updates
    Added a 2020 pivot to the bed leveling z pivots to allow use of 2020.
    [Z-Bed_Leveling_Pivots.scad, z_pivot_2040_v2x1.stl, z_pivot_2040_v3x1.stl]
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2019-05-08 Updates
    Changed x-carriage., a simpler squared off version.
    Added a rear cover to the power switch holder.
    [CoreXY--X-Carriage-wheels-v2.stl, CoreXY--X-Carriage-wheels.stl, CoreXY-X-Carriage.scad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]
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2019-05-28 update
    added nut holes for the extruder and belt mounts on the carriage
    [CoreXY--X-Carriage-wheels-v2.stl, CoreXY-X-Carriage-wheels-v2.stl, CoreXY-X-Carriage-wheels.stl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]
2019-06-15 updates
    Add a one piece x-carriage with front, rear and belt holder. Added the duetwifi sd card files. In poer.scad add a power socket with a seperate switch.
    [CoreXY-X-Carriage-wheels-rrear-v2.stl, CoreXY-X-Carriage-wheels-v2.stl, CoreXY-X-Carriage.scad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]
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2019-08-08 Updates
    Made a titan extruder platform with the filament tension spring in the front for better access.
    [CarriageBeltDrive.stl, CoreXY-MSv1-h.scad, CoreXY-Motor-x2.stl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]
2019-08-17 Updated
    Updated Duet Wifi files. Made my own fan duct for 5150 and you can set the length.
    [CoreXY-X-Carriage.scad, FanDuct65_v2.stl, FanDuct_v2.scad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]
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2020-04-07 Update to use 3mm brass inserts
    Added ability to use brass 3mm inserts.
    Added commented vars for 2mm & 4mm brass inserts in screwsizes.scad.
    [CoreXY-X-Carriage-Front-Brass.stl, CoreXY-X-Carriage.scad, screwsizes.scad]
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2020-04-23 Update
    Fixed CarriageBeltDriveStandAlone()
    [BeltDriveStandalone.stl, CoreXY-X-Carriage.scad]
2020-05-16 Updates
    Printed some of the new parts, and had to fix them.
    [CoreXY-X-Carriage-Front-Brass.stl, CoreXY-X-Carriage-Rear-Brass.stl, CoreXY-X-Carriage.scad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]
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2020-10-27 Update
    Updated photos.
    Brass inserts for the rest of parts.
    Single wirechain from x carrainge to frame. The one on the end of the x axis is still used for the y endstop and led strip.
    [AdjustableBLTHolder.stl, AdjustableBLTMount.stl, AdjustableIRMount.stl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]
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2020-11-08 Update
    Added photos and stl of the parts.
    Updated the MS web cam in CameraMount.scad. Added spacers to use thrust bearing on the z motors.
    [AllInOne X Carriage no extruder.stl, CameraMount.scad, IdlerWasher.scad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]
2020-12-01 Update
    Updated x carraige to have 4 or 5 extruder mount holes. Added a PTFE bracket to be able to use ptfe tubing from spool to titan extruder. Made the singleaero adjustable for the size of the stepper mot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
    [AllInOne X Carriage Aero no extruder.stl, AllInOne X Carriage no extruder.stl, BL_Touch_Aero_V6.stl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]
2020-12-10 Updates
    Camera mount just for a PI camera.
    Added a brace attachment for the TitanAero extruder mount.
    Add mount for a reset button.
    [CameraMount.scad, PICameraMount.stl, ResetButton.scad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]
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2021-04-29 Updates
    Can now use a toggle switch for main power
    Updated some more files for BOSL2
    Added a Berd Air pump holder from thingiverse and tube mount for the hotend.
    Changed the front bearing holders to be adjustable.
    Updated Duet 3 sys and macro zip files
    [Air_Pump_Anti-Shock_Base.stl, Air_Pump_Anti-Shock_Mount.3mf, Air_Pump_Anti-Shock_Mount_.stl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]
2021-09-25 Update
    Added EXOSlide X-Carriage setup
    Added Berdair mount to E3Dv6 heatsink
    Added a Strike X for EXOSLide
    Added a LED strip mount for EXOSlide
    Added a Mean Well P/S mount
    [2020DrillGuide.stl, AdjustableBearingMountMotorMountSet.stl, AllInOne X Carriage Aero no extruder.stl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]
2021-11-04 Changed X to use EXOSLide
    EXOSlide X carriage
    Berdair tube mount to top of E3DV6 heatsink
    Long 30mm to 40mm fan adapter
    [40mmTo30mmFan.scad, BLTouchMountBMG.stl, BerdAirE3DV6.stl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]
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2022-02-27 Update (STL/PNG)
    Updated stls, png and rar files for sys and macros.
    [40mmTo30mmFan.scad, 5150To30mmFan.stl, Cable_bundler.stl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]
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
